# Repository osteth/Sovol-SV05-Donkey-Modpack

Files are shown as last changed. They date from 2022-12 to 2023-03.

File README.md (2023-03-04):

# Sovol-SV05-Donkey-Modpack
A set of modifications to turn a stock Sovol SV05 into a rock solid 3D printing beast of burden. 

## Initial Assembly Notes:
Durring the initial assembly, the manua will tell you to run the extruder wires on the outside of the cube structure. I have found that this causes a lot of issues with not having long enouch cables to reach the front left corner. Instead run the cables to the inside, and ziptie them to the rear just behind the endstop. 

The manual also instructs to install the filament guide upside down from the way it should really work. I flip it over and attach it so the top of the bracket touches the upper corner bracket. 

## Modification Stage 1:

### Notice! - I have since encountered issues with the extruder that prevent the system from printing to my expectations. Please check issues for more info

In stage one we are making the lowest cost/return modsifications only. 

First and foremost, change the firmware, immediately. https://github.com/osteth/Sovol-SV05-Donkey-Modpack/blob/a93c873029fcdde4d4e717f142fba4256eb7f2ac/SV05%20Firmware/HillSoftware%20Octoprint%20Enabled%20Firmware.bin

This is the firmware I am currently using. I found it from https://github.com/hillsoftware/SV05 there may be some updates you can find at that link. 

While purchasing your SV05 I highly reccomend additionally purchasing a bi-metal heatbreak and hardened nozzels. 

https://sovol3d.com/products/bi-metal-heat-break-for-sv04-sv01pro-3d-printer

https://sovol3d.com/collections/nozzles/products/tungsten-nozzles

Sovol Nozzels are not standard V6 nozzels from what I can tell they appear significatly smaller to me.

When replacing the heatbreak I found that my printers had 2 setscrews (one on top of the other) holding the heatbreaks into the housing. 
I am certain if you found this you have also found Aurora tech's video (https://youtu.be/1GrnOgkhclw) which reccomends the same things. I Followed Aurora tech guidance to move the spool up to the top and to add a filament guide. I did not like this because it lead to print failures when the filament would get dragged around the X-axis stepper motor.

~~The Filament guide I designed in at https://github.com/osteth/Sovol-SV05-Donkey-Modpack/blob/a93c873029fcdde4d4e717f142fba4256eb7f2ac/Mods/Sovol%20SV05%20Filament%20Guide.stl if you want to give it a try but know that you may experience some some failures.~~

This is not perfect by any means but its the best I have come up with so far. This turntable spool holder is the best method I have come up wit to date.
https://github.com/osteth/Sovol-SV05-Donkey-Modpack/tree/main/Mods/Turntable%20Spool%20Holder

## Modification Stage 2:
In modification Stage 2 we are going to try to improve quality of life using DIY/self printed mods. 
I started with this video from BV3D https://www.youtube.com/watch?v=BASzPjC3qu0 and then expanded upon their mods to dress the printer up even more.

### Shopping list:

Spring Steel PEI build sheet($23) - https://www.amazon.com/Creality-3D-Magnetic-Platform-235x235mm/dp/B08TGD51HR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

I dont like the Sovol provided floppy sheet. these smooth PEI sheets have WILDLY greater bed adhesion and can PEI can be cleaned with acytone, I clean my bed with acytone after every print because I found that it is the only way to cleanse both finger oils and filament residues from the plate. just as a word of caution, do not use acytone on the Sovol provided sheet, it will destroy it. 

2.85mm Nylon Filament($11) - https://www.amazon.com/dp/B074VRHKF2?psc=1&ref=ppx_yo2ov_dt_b_product_details
We only need a small amount of this filament but its a useful thing to have on hand. This is used inside of the braided wiring sleve that runs out to the extruder and properly strain relieves and gives body/support to the cables so that they cannot get into wrapped around the gantry and causing print failures. 

M3 T-nuts($6) - https://www.amazon.com/dp/B08NZMD2BJ?psc=1&ref=ppx_yo2ov_dt_b_product_details
M5 T-nuts($8) - https://www.amazon.com/dp/B086MKNYDS?psc=1&ref=ppx_yo2ov_dt_b_product_details
These are used to connect things into the frame extrusions. you definitely do not need this many, but this is how I buy them because they are so handy to have on hand. 

Velcro cable ties($13) - https://www.amazon.com/gp/product/B07V1YL6KR/ref=ewc_pr_img_1?smid=A2MDCC74HZMD6T&th=1
You can use regular zip ties if you like, but these are great for 3D printers because I constantly end up having to mess with the cable management from time to time. 

Limit swithes($6) - https://www.amazon.com/dp/B07X142VGC?psc=1&ref=ppx_yo2ov_dt_b_product_details
this is used to DIY a filament sensor. if you dont want to make your own feel free to just purchase a filament sensor outright for about the same price, this is only reasonable to do if you expect to make 10 sensors. 

Metric fasteners set($25)- https://www.amazon.com/dp/B07PJQC7T6?ref=ppx_yo2ov_dt_b_product_details&th=1
If you already have M3 and M5 fasteners just use what you have. If you 3d print, you will need some kit like this.

Filament($25ea) - https://us.polymaker.com/products/polylite-pla-pro?_pos=1&_sid=847d721b9&_ss=r
I use this Polymake PLA pro, and it has served me well. Use whatever you like, but this has worked for me. I think you can do this with about a single spool. It may take 2, I place polymaker orders in 4 spools at a time because that is what the most they ship in a single box.

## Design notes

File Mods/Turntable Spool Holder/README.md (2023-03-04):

# Turntable spool holder
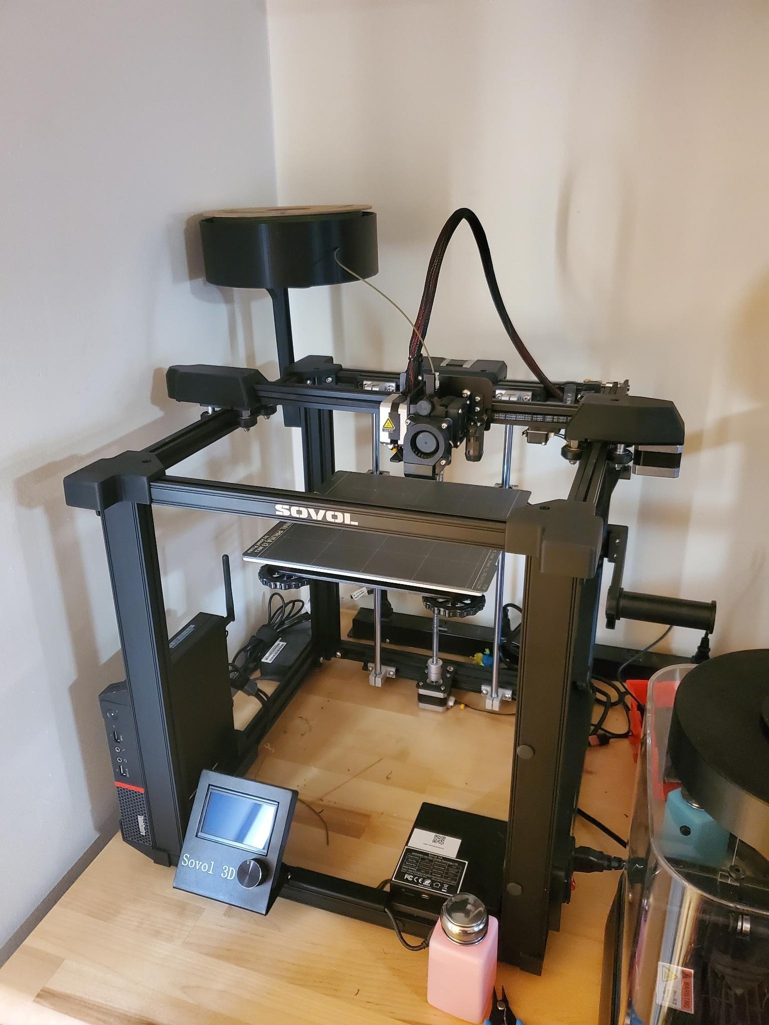
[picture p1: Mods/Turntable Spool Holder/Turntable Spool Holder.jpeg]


https://github.com/osteth/Sovol-SV05-Donkey-Modpack/blob/6bebe50815efbc31729b86ba3ea0b8c5ca4c4fc7/Mods/Turntable%20Spool%20Holder/Turntable%20Spool%20Holder.jpeg

This turns the spool on its side and uses a bearing to reduce drag on the filament to a minimum. 
I use polymaker spools predominantly so I made a spindle for it but it is parametric so you can
resize it easily to meet your needs using the provided fusion360 files. 

I used M3 hardware for the holes and reused the M5 hardware from the stock spool holder to attach
it to the machine. 

I used these cheap 608 skateboard bearings: 
https://www.amazon.com/dp/B07C6FL8TW?psc=1&ref=ppx_yo2ov_dt_b_product_details
As with all of the cheap amazon bearings they are greese filled and dont spin very freely out of the
package. just hit them with isopropyl alchohol and spin them till it comes out and they free spin.
this should not take long to me maybe a minute per bearing. 

I lost a T-nut somewhere along the way and these worked as a replacement )try to avoid the $9 mistake )
https://www.amazon.com/dp/B086MKNYDS?psc=1&ref=ppx_yo2ov_dt_b_product_details

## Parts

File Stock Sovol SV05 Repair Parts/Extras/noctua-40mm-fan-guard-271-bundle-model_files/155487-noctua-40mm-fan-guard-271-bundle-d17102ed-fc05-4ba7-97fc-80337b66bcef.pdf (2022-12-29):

# Noctua 40mm Fan Guard 27+1 Bundle

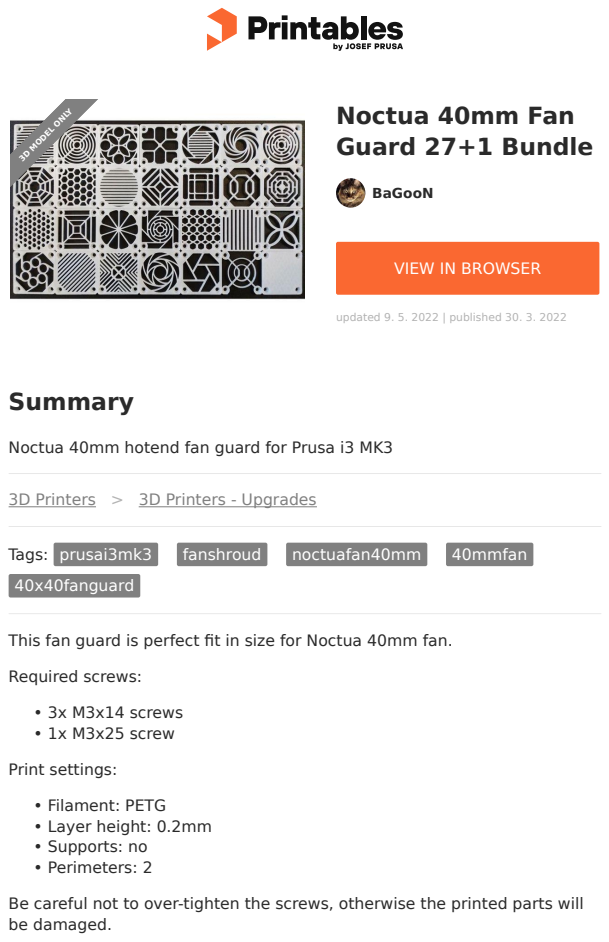
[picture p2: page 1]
Summary; 3D Printers; 3D Printers - Upgrades; Tags: prusai3mk3; fanshroud; noctuafan40mm; 40mmfan; 40x40fanguard; Required screws:; 3x M3x14 screws; 1x M3x25 screw; Print settings:; Filament: PETG; Layer height: 0.2mm; Supports: no; Perimeters: 2; BaGooN; updated 9. 5. 2022 | published 30. 3. 2022; 3D MODEL ONLY

VIEW IN BROWSER (https://www.printables.com/model/155487-noctua-40mm-fan-guard-271-bundle)

Noctua 40mm hotend fan guard for Prusa i3 MK3

This fan guard is perfect fit in size for Noctua 40mm fan.

Be careful not to over-tighten the screws, otherwise the printed parts will
be damaged.

# Model files

# This remix is based on

40mm Fan Guard (https://www.printables.com/model/147825-40mm-fan-guard)

by BaGooN (https://www.printables.com/social/174466/about)

40mmfanguard_1-v3.stl

40mmfanguard_2-v1.stl

40mmfanguard_3-v1.stl

40mmfanguard_4-v1.stl

40mmfanguard_5-v1.stl

40mmfanguard_6-v1.stl

40mmfanguard_7-v1.stl

40mmfanguard_8-v1.stl

40mmfanguard_9-v1.stl

40mmfanguard_10-v1.stl

40mmfanguard_11-v1.stl

40mmfanguard_12-v1.stl

40mmfanguard_13-v1.stl

40mmfanguard_14-v1.stl

40mmfanguard_15-v1.stl

40mmfanguard_16-v1.stl

40mmfanguard_17-v1.stl

40mmfanguard_18-v1.stl

40mmfanguard_19-v1.stl

40mmfanguard_20-v1.stl

40mmfanguard_21-v1.stl

40mmfanguard_22-v1.stl

40mmfanguard_23-v1.stl

40mmfanguard_24-v1.stl

40mmfanguard_25-v1.stl

40mmfanguard_26-v1.stl

40mmfanguard_27-v1.stl

- You set infill own way want to make it.

# License

This work is licensed under a

Creative Commons (4.0 International License)

Attribution (http://creativecommons.org/licenses/by/4.0/)

✖ | Sharing without ATTRIBUTION
✔ | Remix Culture allowed
✔ | Commercial Use
✔ | Free Cultural Works
✔ | Meets Open Definition

40mmfanguard_99-v1.stl

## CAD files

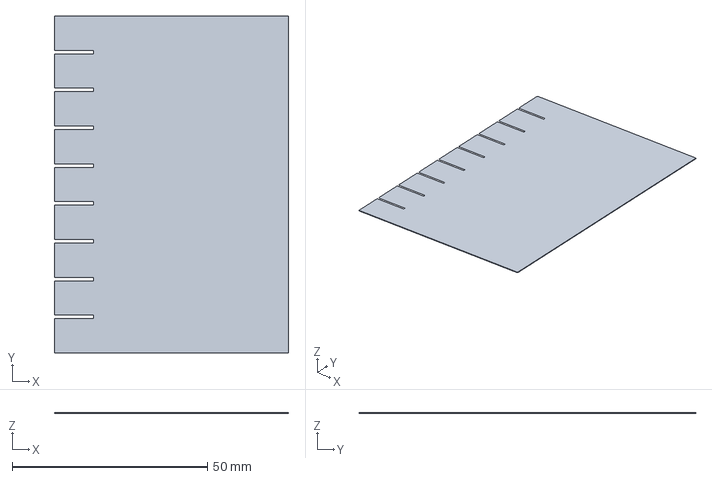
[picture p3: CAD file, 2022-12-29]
Calibration/FirstLayerCalibration-FirstLayer.3mf
60.0 x 86.4 x 0.2 mm

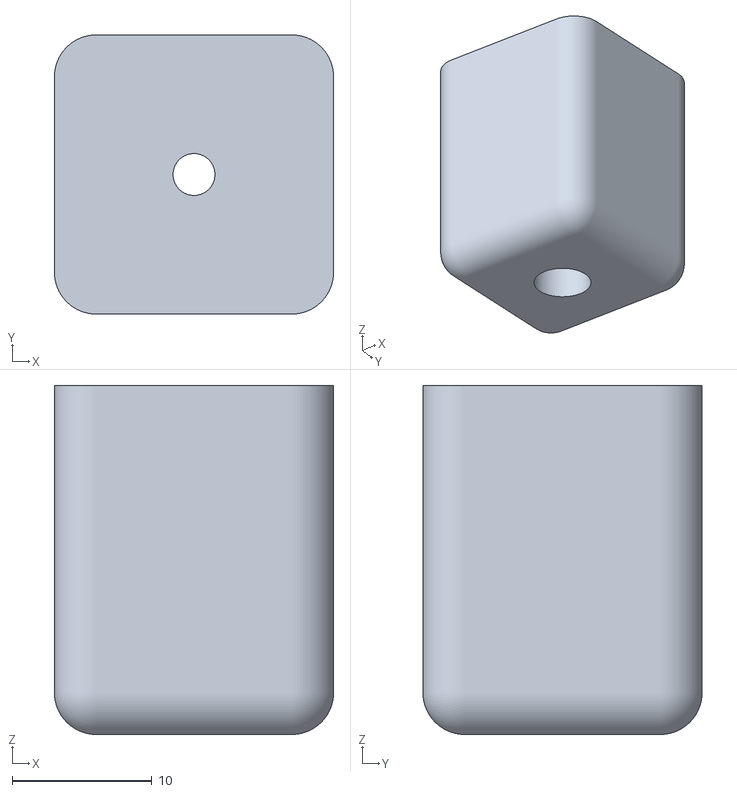
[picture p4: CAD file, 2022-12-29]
Mods/2020 Extrusion USFF computer mount/Inner Block.stl
20.0 x 20.0 x 25.0

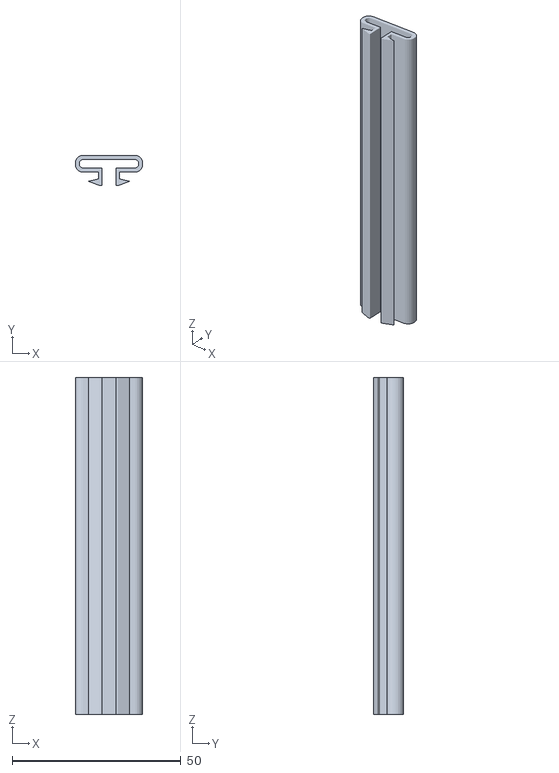
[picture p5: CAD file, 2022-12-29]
Mods/Statge 2/Cable Guides for 2020 extrusion/Cable Guide 5x100mm.stl
20.0 x 9.00 x 100.0

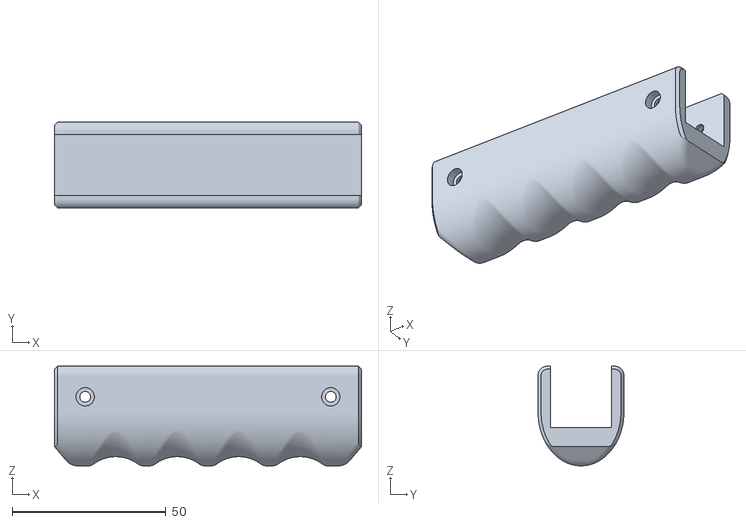
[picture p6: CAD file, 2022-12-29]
Mods/Statge 2/Carry Handles/Grip_2in1_v1.1.stl
100.0 x 28.0 x 32.5

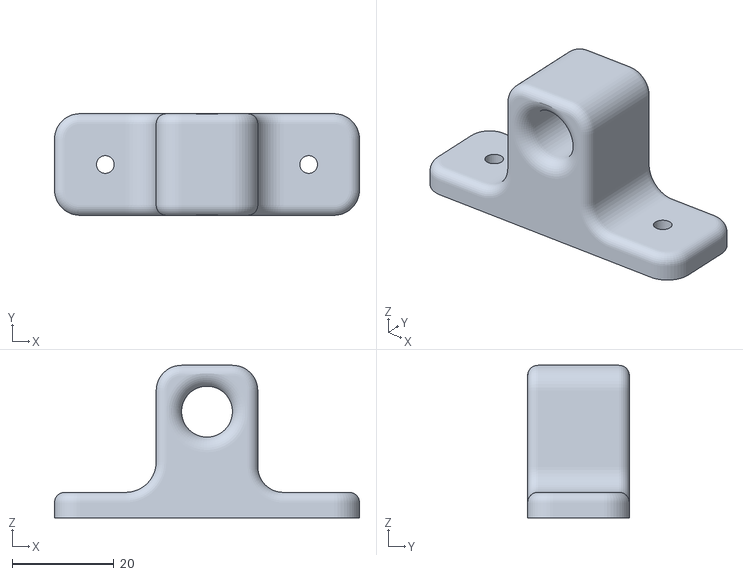
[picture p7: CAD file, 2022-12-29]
Mods/Statge 2/Sovol SV05 Filament Guide.stl
60.0 x 20.0 x 30.0

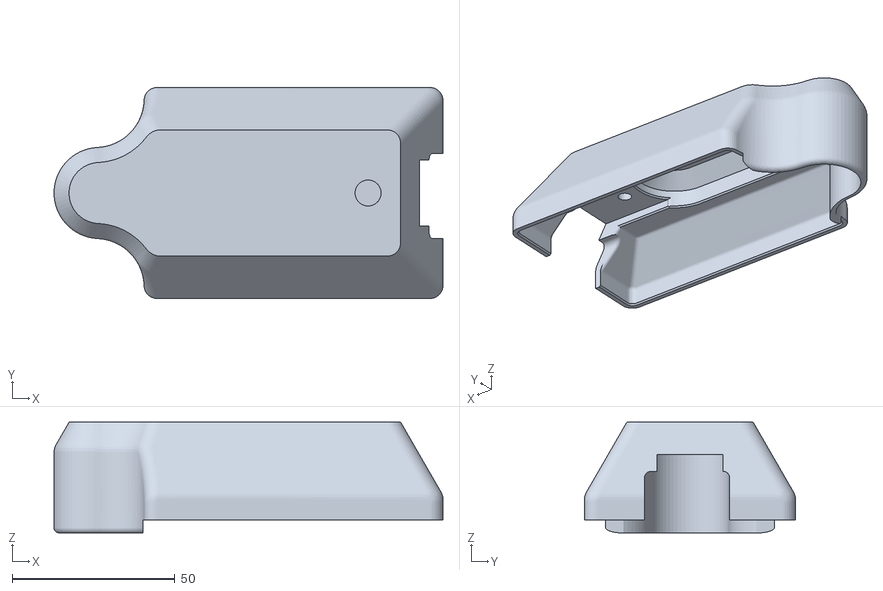
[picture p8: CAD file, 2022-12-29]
Mods/Statge 2/X-Axis_belt_cover/Sovol SV05 X-Axis Gantry Cover Left .stl
119.5 x 64.8 x 34.0

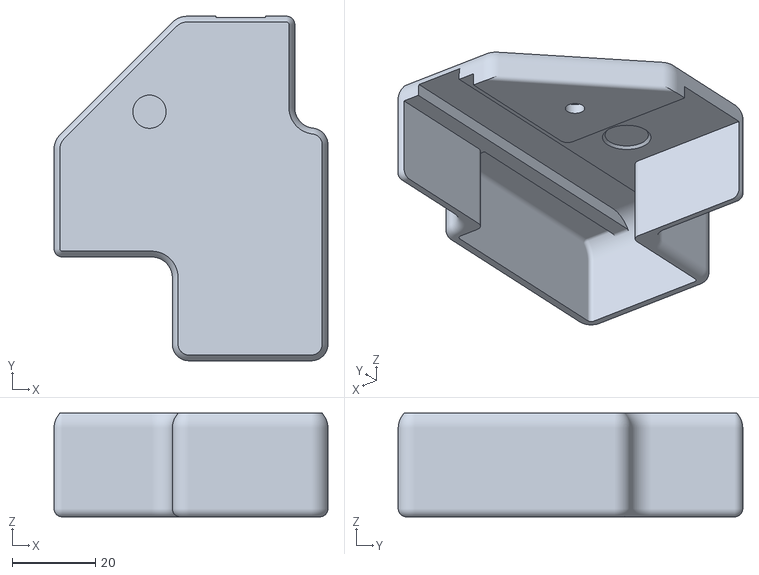
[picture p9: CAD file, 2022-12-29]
Mods/Statge 2/Y-Axis-belt-covers with silent-home-Y Endstop/front_right_cover.stl
66.0 x 83.0 x 25.0

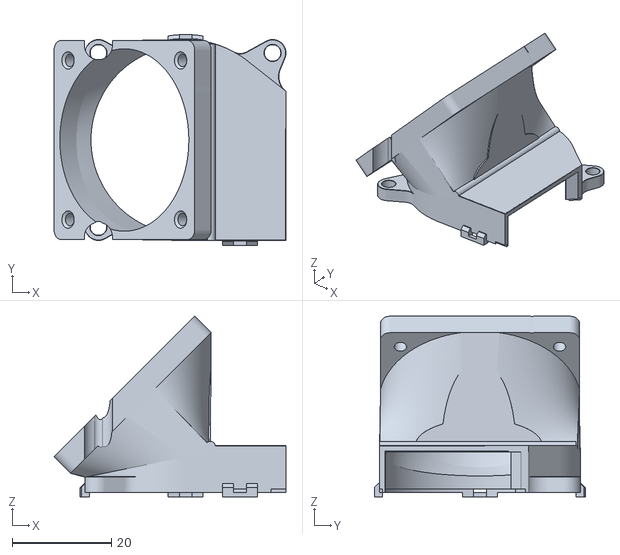
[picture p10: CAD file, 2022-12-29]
Mods/SV05 Noctua Fan Mod/Sovol SV05 Noctua fan mod horn.stl
46.6 x 42.4 x 36.3

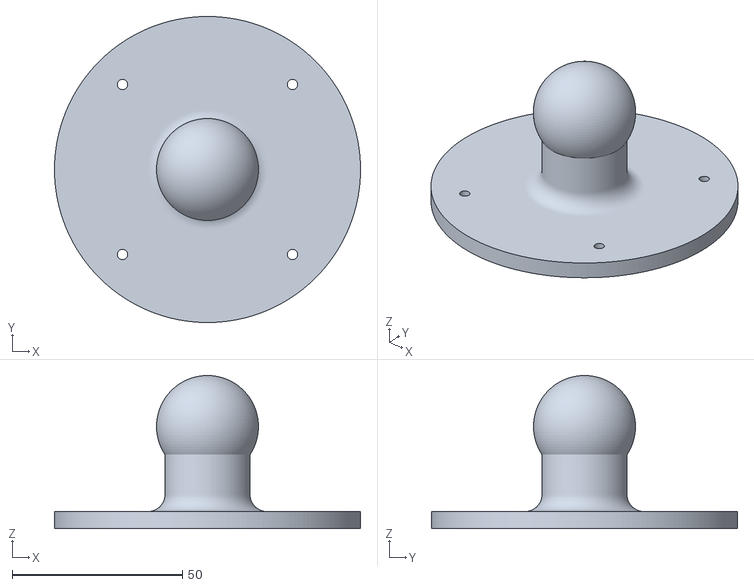
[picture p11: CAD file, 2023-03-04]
Mods/Turntable Spool Holder/STLs/Spool Holder Lid Knob.stl
90.0 x 90.0 x 45.0

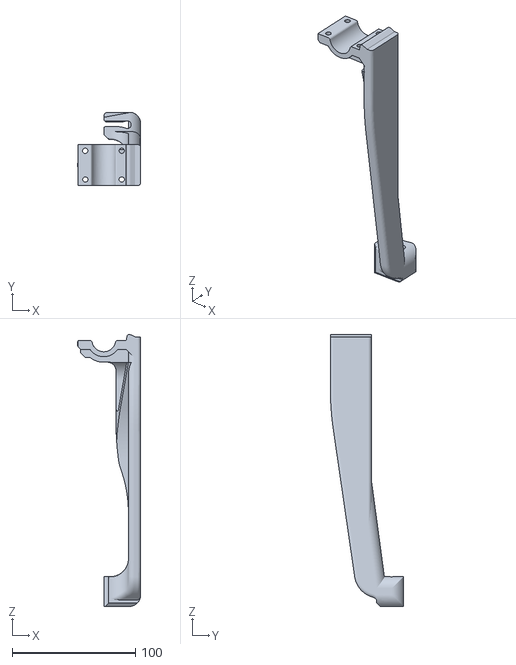
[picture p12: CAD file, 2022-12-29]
Stock Sovol SV05 Repair Parts/Bed Support Arms/Bed Support arm right.stl
51.5 x 59.5 x 221.0

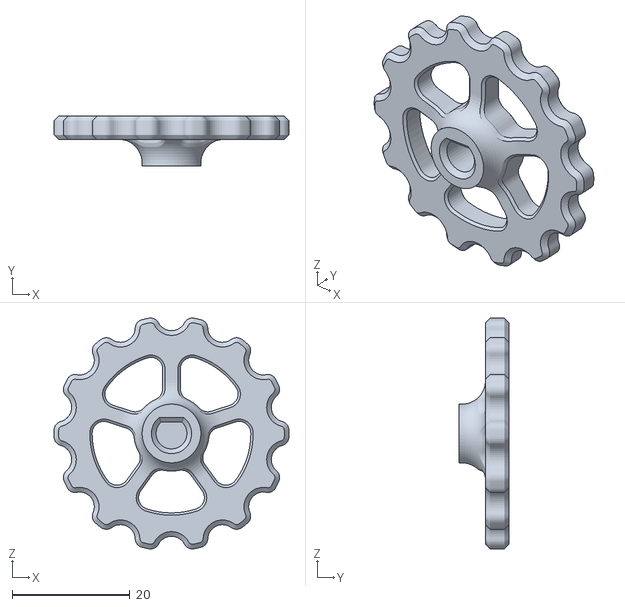
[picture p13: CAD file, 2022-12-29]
Stock Sovol SV05 Repair Parts/Bed Tramming Knobs.stl
40.0 x 8.50 x 39.3

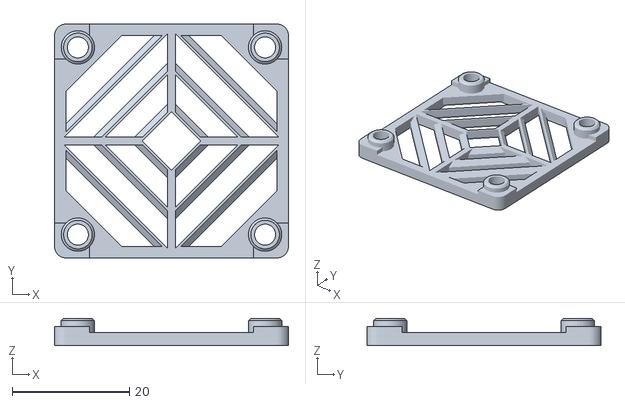
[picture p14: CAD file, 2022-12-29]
Stock Sovol SV05 Repair Parts/Extras/noctua-40mm-fan-guard-271-bundle-model_files/40mmfanguard_11-v1.stl
40.0 x 40.0 x 4.70

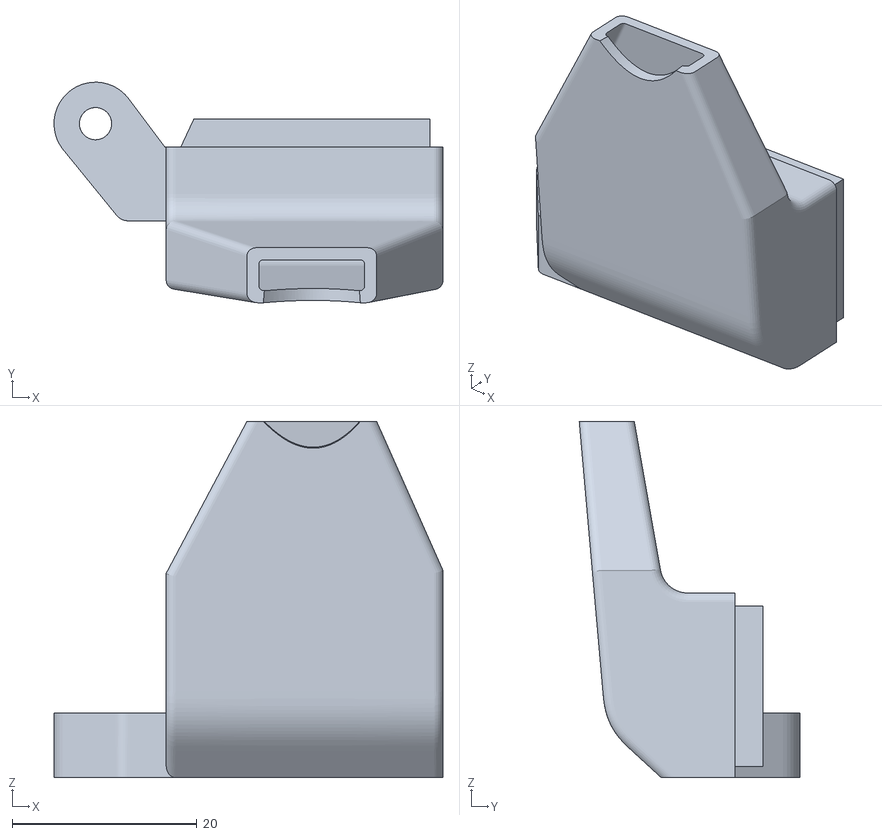
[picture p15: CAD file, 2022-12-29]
Stock Sovol SV05 Repair Parts/Part Cooling Fan Ducts/Sovol fan duct narrow.stl
42.1 x 23.9 x 38.6

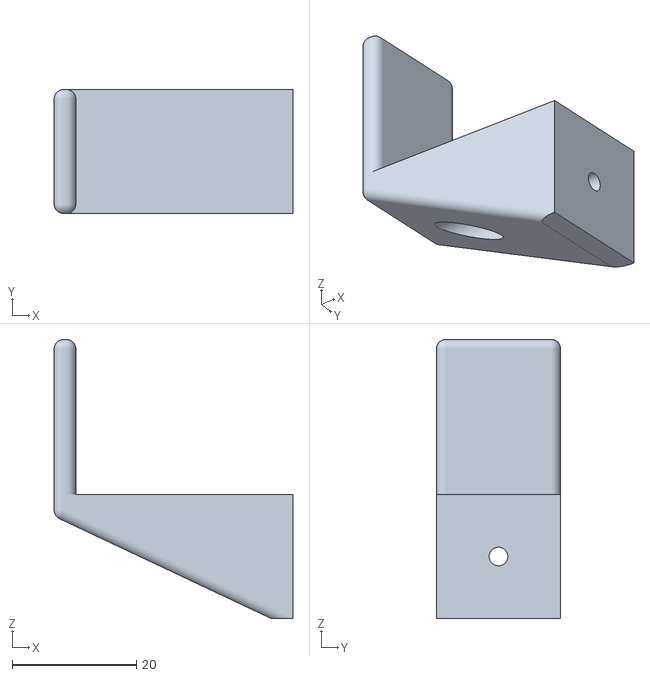
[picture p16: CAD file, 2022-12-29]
Mods/2020 Extrusion USFF computer mount/Mounting Bracket.stl
38.5 x 20.0 x 45.0

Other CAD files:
Mods/Statge 2/Cable Guides for 2020 extrusion/Cable Guide 15x100mm.stl
Mods/Statge 2/Carry Handles/Grip_v1.1.stl
Mods/Statge 2/Sovol Sv05 Bed Strain Relief.stl
Mods/Statge 2/X-Axis_belt_cover/Sovol SV05 X_Axis Gantry Cover Right.stl
Calibration/FirstLayerCalibration-FirstLayer.stl
Mods/SV05 Noctua Fan Mod/Sovol SV05 Noctua fan mod base.stl
Mods/Statge 2/20x20 Extrusion endcap.stl
Mods/Statge 2/90_Degree_Brace_for_2020_Extrusion_Small_4bolt.stl
Mods/Statge 2/Cable Guides for 2020 extrusion/Cable Guide 10x100mm.stl
Mods/Statge 2/Cable Guides for 2020 extrusion/Cable Guide 20x100mm.stl
Mods/Statge 2/Cable Guides for 2020 extrusion/Cable Guide 7.5x100mm.stl
Mods/Statge 2/Cable Guides for 2020 extrusion/Sovol SV05 Rear Cable Cover 180mm.stl
Mods/Statge 2/Clip On Display Rear Cover No Screws/Ender_3_Beeper_Cap.stl
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

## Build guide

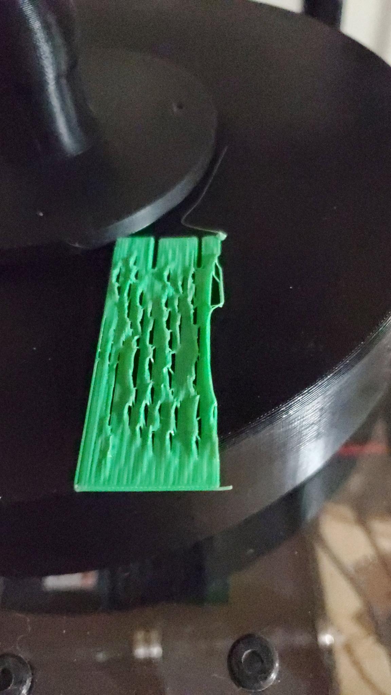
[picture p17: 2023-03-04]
Troubleshooting/printing_WAY_too_HOT.jpeg

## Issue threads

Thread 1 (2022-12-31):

Extruder inconsistency makes it impossible to calibrate steps/mm

osteth, 2022-12-31:
After testing with both units the stock extruder does not appear to be sufficient to produce dimensionally accurate prints.
used https://makershop.co/3d-printer-extruder-calibration-steps/ and th3dstudio.com/estep-calculator/ to attempt to calibrate Esteps and could not accomplish calibration.
No matter how high I raised the steps/mm I could not make it extrude 100mm of filament.  Additionally, I got different error values by extruding 100mm all at once vs extruding 10x 10mm extrusions.

Investigate extruder alternatives.

toklok, 2023-03-03:
> After testing with both units the stock extruder does not appear to be sufficient to produce dimensionally accurate prints. used https://makershop.co/3d-printer-extruder-calibration-steps/ and th3dstudio.com/estep-calculator/ to attempt to calibrate Esteps and could not accomplish calibration. No matter how high I raised the steps/mm I could not make it extrude 100mm of filament. Additionally, I got different error values by extruding 100mm all at once vs extruding 10x 10mm extrusions.
>
> Investigate extruder alternatives.

Any word?  I just purchased one of these machines.

osteth, 2023-03-04:
The problem is definitely still there. I have got my machine to where it can print anything that does not require dimensional accuracy by making a few changes.
First: I made a turntable style spool holder - https://github.com/osteth/Sovol-SV05-Donkey-Modpack/tree/main/Mods/Turntable%20Spool%20Holder
This takes the drag off the filament and resolves a lot of the issues.

Second: I reduce the temperatures SIGNIFICANTLY Im printing at 185 for the first layer and 180 for the rest of the print. I can only assume that my thermocouple is improperly calibrated or something??
If your first layer looks like this picture then your having the same issue and have to dial the heat way back.
https://github.com/osteth/Sovol-SV05-Donkey-Modpack/blob/main/Troubleshooting/printing_WAY_too_HOT.jpeg

Finally: I am slowly trying out different hot ends. I am currently working on swapping a Hemera Revo onto my test machine but the Sovol is just different enough from the ender5 to make this difficult.  I have I think 5 hot ends of various price points. The plan is to swap to a known good and then dial back until failure.

I have additionally had issues with the hotend being pulled upwards away from the bed out towards the corners from the cables and filament pulling tension against it and it cams up significantly enough to cause first-layer adhesion failure so I can really only print in the center ~50% of the build plate.

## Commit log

2022-12-29 Initial Release
    Initial release of my collection of SV05 files.
    [20x20 Extrusion endcap.stl, 40mmfanguard_1-v3.stl, 40mmfanguard_10-v1.stl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]
2023-03-04 Add Turntable spool holder
    [20x20 Extrusion endcap.stl, 90_Degree_Brace_for_2020_Extrusion_Small_4bolt.stl, Cable Guide 10x100mm.stl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]
